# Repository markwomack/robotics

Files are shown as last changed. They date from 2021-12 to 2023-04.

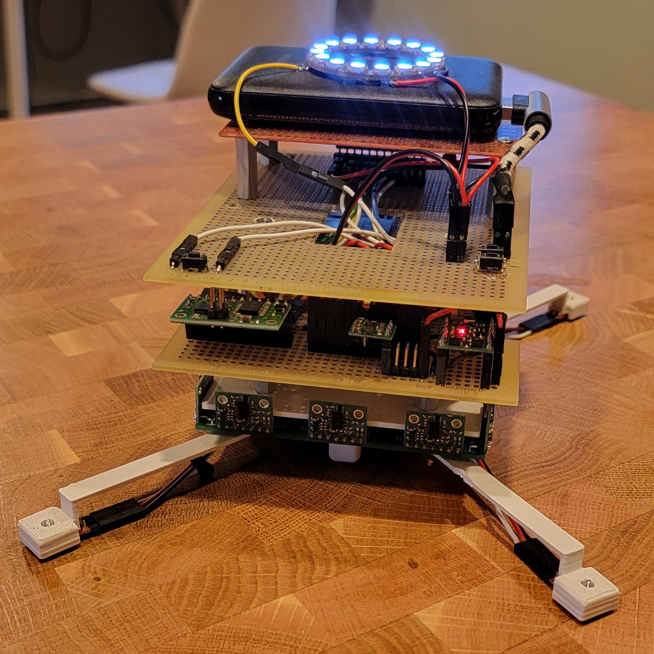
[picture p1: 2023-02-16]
robot_mark_ii/images/Beatrice_Portrait.jpg

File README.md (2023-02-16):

# robotics
The project stores the various designs, documentation, and code for my robots.

## ard_lib
This directory contains Arduino libraries that I have written and that I use in my robotics sketches. You can copy the directories in this folder to the Arduino "Libraries" directory and restart the Arduino IDE. Please see the [DEPENDENCIES](https://github.com/markwomack/robotics/blob/main/DEPENDENCIES.md) file for other Arduino library dependencies.

## robot_mark_ii
This directory contains all the Arduino sketches that I have written for my "Robot Mark II", the second robot iteration that I have built. The codename for this robot is "Beatrice". There are many test sketches to test the connections and functionality of the various sensors and motors. The "base_sketch" is the main sketch that has the behaviors I have written to run useful things on the robot.

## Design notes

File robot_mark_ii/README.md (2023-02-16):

# Robot Mark II 'Beatrice'
<p>This is the directory that contains all of the code and designs specific to the
Robot Mark II 'Beatrice'.</p>

* Beatrice is an all-around robot with many different
sensor sets that allow it to detect table edges, objects that are close by,
and lines that are placed on a table or floor.

* It is a differential drive robot
with motor encoders. This means that it has software control for the motor power
(PID) so that the motors perform at an expected rate of speed.

* The framework provided from using the
[Task Manager library](https://github.com/markwomack/TaskManager) and implemented
support classes means that it can be easily extended to perform different
behaviors.

* Printing debug messages to a remote computer allows for basic feedback when
debugging new bahaviors. This is done by using UDP over WiFi with the
[Arduino Logging library](https://github.com/markwomack/ArduinoLogging).

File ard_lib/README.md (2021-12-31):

# ard_lib
This is a collection Arduino libraries used for the robotics sketches. Copy them to the Arduino Libraries directory and then re-launch the Arduino IDE.

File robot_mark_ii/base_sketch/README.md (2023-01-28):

# Base Sketch

This is the base sketch for the Mark II 'Beatrice' robot that supports all of the behaviors
it has been programmed to perform. Beatrice is meant to be an all-around robot for 
different challenges such as the
[HBRC TableTop and A-Mazing LineBot challenges](https://www.hbrobotics.org/index.php/challenges/).
Beatrice is still a work-in-progress, and more behaviors will be added as they are
implemented.

## Files

### base_sketch.ino
<p>This sketch is the base of the program. It sets up all of the sensors, motors,
and leds that will be used on the robot. It creates the specific BehaviorTask that
will be executed, and uses the Task Manager to monitor a button to start/stop the
robot execution.</p>

### robot_constants.h
<p>This file contains the constants related to the robot, mostly physical constants
like the number of encoder ticks per wheel revolution, etc.</p>

### pin_assignments.h
<p>This file contains all of the Teensy 3.5 pin assignments used throughout the
code.</p>

### Behaviors
<p>The robot can be programmed to execute 'behaviors'. These behaviors can be anything
that it can use its sensors and output controls to perform.</p>

#### BehaviorTask
<p>The BehaviorTask is the base class for all of the behaviors that can be executed
on the robot. It has common members and methods that can be used by all subclasses
to implement their specific behavior.</p>

#### StayOnTableTopTask
<p>The StayOnTableTopTask is the behavior that will keep the robot on the table and
not fall off. Once it finds a table edge, the robot will go back and forth on the table.
It passes
[Phase 1 of the HBRC TableTop Challenge](https://www.hbrobotics.org/index.php/challenges/).</p>

#### PushOffTableTopTask
<p>The PushOffTableTopTask is the behavior that will search for an object, and when found
it will proceed to push the object off of the table. After pushing off the table, the
robot will do a happy dance and then wait to be activated again. It passes
[Phase 2 of the HBRC TableTop Challenge](https://www.hbrobotics.org/index.php/challenges/).</p>

### Sensors and Controls
<p>The robot has a number of sensors and output controls that it can use from its behaviors.</p>

#### EdgeSensors
<p>Edge sensors are used to detect the edges of the table, and are the four IR sensors located on
the four arms that come from the corners of the robot. The EdgeSensor class defines the methods
that can be used to initialize and access the sensor values.</p>

#### DistanceSensors
<p>Distance sensors are the ten sensors that ring the robot, two sets of 5. These are ToF
sensors that return a distance when an object is close. The DistanceSensors class defines the
methods that can be used to initialize and access the sensor values.</p>
  
#### MotorsAndEncoders
<p>There are two motors on the robot, each with its own encoders to know how far a wheel has
turned and thus how far the robot has travelled. The MotorsAndEncoders class defines the
methods that can be used to initialize and control the motors and encoders.</p>

#### PixelRing
<p>The robot has an Adafruit NeoPixel ring installed that can be used to indicate state
by the behavior implementation. The PixelRing class defines the methods and to
initialize and control the pixel ring.</p>

#### SurfaceSensors
<p>There are 10 surface sensors on the bottom of the robot. These are meant to detect things
on the surface of the table, such as lines of black tape. The SurfaceSensors class defines
the methods to initialize and access the sensor values.</p>

### Support Tasks
<p>There are a number of tasks used by the behavior tasks to help in reading sensors or
updating output controls. Each behavior task implementation can install whichever support
tasks it needs.</p>

#### AdjustMotorSpeedTask
<p>The AdjustMotorSpeedTask is called periodically to allow the motor PID controls, found
in the MotorsAndEncoders class, to adjust the power to the motors so that the target
speed is maintained.</p>

#### AdjustPixelRingTask
<p>Many of the defined patterns that can be shown on the PixelRing are animated. The
AdjustPixelRingTask allows the PixelRing to update its LEDs.</p>

#### ReadEdgeSensorsTask
<p>The ReadEdgeSensorsTask allows the robot to periodically read the values of the
edge sensors.</p>

### Miscellaneous

#### NetworkHub
<p>Optionally, the robot can be connected to WiFi to aid in debugging. The NetworkHub class
is used to connect to a WiFi network. The WiFi netword name and login credentials are stored
in the file secrets.h.</p>

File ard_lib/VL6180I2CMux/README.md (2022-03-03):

# VL6180I2CMux
<p>The VL6180I2CMux library provides code for accessing and managing the custom PCB used to manage up to 5 VL6180X Time-of-flight
  I2C distance sensors on an I2C bus. The VL6180X sensors use a single I2C address, and will conflict one another if placed on the
  same I2C bus. To remedy this situation, a simple multiplexer ship is used on the custom PCB to allow for a single sensor to be
  active at any time. Simply select the sensor you want to access before accessing it. In addition, the VL6180I2CMux library contains
  methods for accessing the sensor. However, once selected, you should be able to access the sensor on the I2C bus as you would normally.</p>

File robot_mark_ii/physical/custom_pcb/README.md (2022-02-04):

# Custom PCBs

This directory has files for custom PCBs used in the build of the Mark II 'Beatrice' robot.

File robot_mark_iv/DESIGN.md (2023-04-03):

# Design - Robot Mark IV 

This document outlines the design of the Mark IV robot.

## Components

These are the major components that make up the robot. This list does not have incidentals like protoboards, sockets, pins,
spacers, connectors, and wires.

- microcontroller tbd
- motorcontroller tbd
- 
- 2 - [Pololu Micro metal gear motor MP 6v 150:1](https://www.pololu.com/product/2382)
- 1 - [Pololu Gearmotor bracket (pair)](https://www.pololu.com/product/989)
- 1 - [Pololu Wheel 70x8mm (pair)](https://www.pololu.com/product/1425)
- 1 - [Pololu Magnetic encoder kit (pair)](https://www.pololu.com/product/4760)
- 2 - [Pololu 6-pin Single-ended Female cable (JST-SH)](https://www.pololu.com/product/4762)
- 2 - [Pololu 4mm x 15 IR sensors](https://www.pololu.com/product/4115)
-  distance sensors TBD
- 1 - [3000mAh Slim USB power bank](https://www.amazon.com/gp/product/B07K9HJR4X/)
- 1 - [USB C U Shape Adapter](https://www.amazon.com/gp/product/B09ZHFWZR9/)
- 1 - [Adafruit AirLift ESP32 WIFI Co-Processor](https://www.adafruit.com/product/4201)

Possible touchscreens:

[https://www.waveshare.com/2.13inch-Touch-e-Paper-HAT.htm](https://www.waveshare.com/2.13inch-Touch-e-Paper-HAT.htm)

[https://www.adafruit.com/product/2478](https://www.adafruit.com/product/2478)

### Chassis

### Microcontroller

### Motor controller

### Motors and encoders

### Power

### WIFI (optional, but recommended)

### Sensors

#### Distance Sensors

#### Line Tracking Sensors

### Robot Control

### State display

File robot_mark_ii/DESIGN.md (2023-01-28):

# Design - Robot Mark II - 'Beatrice'

This document outlines the design of the Mark II 'Beatrice' robot.

## Components

<p>These are the major components that make up Beatrice. This list does not have incidentals like protoboards, sockets, pins,
spacers, connectors, and wires. A wiring diagram is be provided, but how the components and wiring is arranged is left as
an exercise to the reader.</p>

- [Teensy 3.5 microcontroller](https://www.pjrc.com/store/teensy35.html)
- [Pololu Qik 2s9V1 motor controller](https://www.pololu.com/product/1110)
- [Polulu Micro metal gearmotor 12v 250:1 (2)](https://www.pololu.com/product/3055)
- [Pololu magnetic motor encoders (2)](pololu.com/product/2598)
- [Pololu 32x7mm wheels (2)](https://www.pololu.com/product/1087)
- [Pololu Gearmotor brackets (2)](https://www.pololu.com/product/1089)
- [Pololu Mini pushbutton power switch](https://www.pololu.com/product/2808)
- [Pololu 5v step-up/step-down voltage regulator](https://www.pololu.com/product/2119)
- [Pololu 7.5v step-up voltage regulator](https://www.pololu.com/product/4014)
- [Pololu IR sensors (4 total for edge detection)](https://www.pololu.com/product/2459)
- [Poloul IR sensors (2 total for line detection)](https://www.pololu.com/product/961)
- [Pololu VL6180X Time-of-Flight Distance Sensor (10)](https://www.pololu.com/product/2489)
- [Adafruit NeoPixel ring 16x5050](https://www.adafruit.com/product/2855)
- [5v power bank battery](https://www.amazon.com/gp/product/B07K6HJTK2)
- [USB cable slim connector](https://www.amazon.com/gp/product/B01MZ8RA3A)
- [Pololu mini pushbutton switch (2)](https://www.pololu.com/product/1400)
- [Adafruit AirLift ESP32 WIFI Co-Processor](https://www.adafruit.com/product/4201)

### Chassis

<p>The chassis is a collection of 3D printed parts for the mounted sensors, a couple of custom PCB boards, and several protoboards
  all put together to form the body of the robot. The chassis is designed to be symmetrical along the axis of the differential drive
  wheels. The profile and sensors of the robot are the same, front to back, flipping on the wheel axis. One side has been arbritrarily
  chosen to be the 'front', but future coding could treat each side equally, eliminating any need for the robot to turn around,
  instead just switching the 'front' in the software.</p>
  
### Microcontroller

<p>The Teensy 3.5 is the heart of the robot. It drives all of the sensors and behaviors.</p>
<p>The Teensy has been modified to use it's own power supply instead of relying on power from the USB port. This is [documented
  here](https://www.pjrc.com/store/teensy35.html) on the back side of the pinout card (see the "VIN separated from VUSB" note). 
  Be sure to do this when assembling the robot.</p>
<p>As of today the Teensy 3.5 may be discontinued (though I have been able to find it at a local MicroCenter). The newer
  Teensy 4.1 is almost a drop in replacement, however there are two issues to be aware of. First, while the Teensy 4.1 has the
  same pin form factor, but the pins are arranged differently. You will have to take this into account when wiring, and the 
  pin_assignments.h file in the code will need to be updated accordingly. Second, the Teensy 4.1 pins are NOT 5v tolerant as 
  they are for the 3.5. You will have to use 3.3v for all of the connections, and will need to have a 3.3v voltage regulator
  instead of the 5v voltage regulator. [Pololu provides a 3.3v voltage regulator](https://www.pololu.com/product/2122).
  Though I have not tried it as of yet, all of the electronic components should function correctly using 3.3v instead of 5v.</p>

### Motor controller

<p>The Pololu Qik 2s9v1 motor controller is a simple to use controller that can drive two motors. It uses a serial port to
  receive motor commands, and one of the Teensy serial ports is dedicated to the Qik. While the controller run on 5v,
  it provides for a separate power source to the motors, which on this robot is 7.5v (see Power section below).</p>

### Motors and encoders

<p>The Pololu micro metal gearmotors can handle up to 12v, but Beatrice runs them with just 7.5v. The motors have a 250:1
gear ratio, which will provide a lot of torque to the wheels to help Beatrice get over bumps and ridges. With the mini 
magnetic encoders having 12 ticks per shaft revolution with the 250:1 gear ratio, there will be 3000 ticks per wheel
revolution. This will provide a high level of accuracy in the odometry.</p>
<p>Beatrice uses a differential drive centered in the chassis. This allows the robot to move forward, backward, turn, and
  spin in place.</p>

### Power

<p>The power to Beatrice is provied by a 5v power bank connected via a modified USB cable to the 5v pushbutton power switch.
The power bank can provide up to 2A of current. The pushbutton switch provides reverse voltage protection. The power flows to
the robot from the switch to two different voltage regulators. The 5v regulator provides power to all of the electronics:
the Teensy, the Qik, and all of the sensors. The 7.5v regulator steps up the 5v to 7.5v to provide more power to the motors.
The 7.5 regulator is connected to the Qik motor controller, which passes the power to the motors.</p>
<p>The 5v regulator can deliver up to 1A in current which is more than sufficient for the electronics. The 7.5v regulator
can provide up to 3A current which much greater than the motor stall current of .75A (1.5A for both motors combined).</p>

### WIFI (optional, but recommended)

<p>Beatrice connects to the internet via the Adafruit ESP32 WIFI Co-Processor breakout board. It is connected to the Teensy
  through the SPI interface, and a custom Adafruit version of the Arduino WiFiNINA library is used to allow different pin
  locations. The internet connection is used to send debugging messages to a remote console, which greatly aids in the
  writing and debugging of robot behaviors. It is much harder to sense objects or program movement with a USB cable
  connected to the back of the robot's Teensy. However, this portion of the build is optional, but greatly recommended.
  Please see the ArduinoLogging library for an example of a setup on a remote computer to receive messages from the robot.</p>

### Sensors

<p>Beatrice is outfitted with different sets of sensors, each for a different purpose.</p>

#### Edge Sensors

<p>Extending out from each corner of the robot are 4 Pololu IR sensors, one for each corner. These are meant to detect
  edges of the tabletop on which the robot is operating. There is no special calibration performed for these sensors.
  Once the value goes above a certain threshold and 'edge' is detected. Each sensor is directly connected to a pin on
  the Teensy, which reads the value periodically when required by the behavior.</p>

#### Distance Sensors

<p>Wrapping around the robot are 10 VL6180X Time-of-Flight distance sensors (3 front, 3 rear, 2 right, 2 left). These
  are meant to detect objects in proximity to the robot. The maximum range of the VL6180X is 60cm, but in practice it
  is more in the 20-30cm range. Each sensor is an I2C device, and values are requested and read using the I2C bus.
  Unfortunately, each sensor hasthe same I2C address, which in turn requires a Multiplexer chip to select the specific
  sensor before interacting with it. For Beatrice this is done using a custom PCB board that is designed to have the
  multiplexer chip and 5 sensors mounted directly on the board. The board is then incorporated into the body of
  the chassis. There is one PCB for the front, and one PCB for the rear, with matching configurations. A separate
  I2C bus and set of selector pins on the Teesny are used to control each board in turn. While the sensors could be
  configured to run in 'continous' mode, currently the code samples distance measurements as needed for the specific
  task in hand. This avoids a periodic task running over its alloted time to execute, and overlapping signals each
  sensor sends out to measure distance. Future code could be written to better time the measurments for each
  sensor so that they do not intefere with each other.</p>

#### Line Tracking Sensors

<p>Underneath the robot, mounted on a 3D printed under-carriage, are more Pololu IR sensors. These are meant to detect
  line patterns on the tabletop or a maze. There are 10 sensors in total, arranged in lines: 2 at the front, 6 across
  the center, and 2 more at the rear. This arrangement makes detecting horizontal and vertical line patterns more
  efficient. Similar to the edge sensors, each sensor is connected to a pin on the Teensy. However, unlike the edge
  sensors, the line sensors require some level of calibration before use to detect lines. While calibrating, the robot
  needs to be moved over the lightest and darkest values found on the tabletop or maze. Once the calibration is completed,
  the calibrated values will then be used in detecting lines.</p>

### Robot Control

<p>The 5v pushbutton power switch will turn Beatrice on and off, but there are is another button to actually control
  the start and stop of the robot behavior. Beatrice uses the TaskManager library to monitor a pin on the Teensy that
  is connected to this pushbutton. When first turned on Beatrice will be in idle mode, with the PixelRing pulsing white.
  When the pushbutton is pressed, the programmed behavior will start. When the pushbutton is pressed again, the behavior
  will be stopped. Pushing the button again will start the behavior, now initialized to forget the previous execution.</p>
<p>Because Beatrice can perform several different behaviors, there is another push button that can be used to select the
  behavior to execute next time the start button is pressed. Each behavior type is numbered, and when selecting, the
  selected behavior number is displayed on the PixelRing by the matching number of LEDs.</p>
  
### State display

<p>Beatrice uses the Adafruit PixelRing to display its current state. When idle it will pulse white. While running it will
  update the PixelRing as it executes the behavior.

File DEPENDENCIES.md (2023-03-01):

# Dependencies

## Third Party Dependencies
The sketches and libraries have dependicies on some third party libraries.

- [MotorAndEncoderManager](https://github.com/markwomack/MotorAndEncoderManager) - Used
  drive the motors and encoders on the robots.
- [Pololu Qik controller](https://github.com/pololu/qik-arduino) - One of the motor
  controllers used.
- [Pololu VL6180X sensors](https://github.com/pololu/vl6180x-arduino) - The distance
  sensors used.
- [Pololu QTR sensors](https://github.com/pololu/qtr-sensors-arduino) - The edge and
  surface sensors used.
- [Adafruit NeoPixel](https://github.com/adafruit/Adafruit_NeoPixel) - The hardware used
  to communicate state.
- [Adafruit WiFiNINA](https://github.com/adafruit/WiFiNINA) - WiFi connction used for
  debugging purposes<br/>
**^^ MUST ^^** use the above version to allow different pin locations
- [PID controller](https://github.com/br3ttb/Arduino-PID-Library) - Used to precisely
  control the motor speeds.
- [PixelRingAnimator](https://github.com/markwomack/PixelRingAnimator) - Provides
  animations to run on the NeoPixel ring.
- [ArduinoLogging](https://github.com/markwomack/ArduinoLogging) - Used to print debug
  messages.
- [TaskManager](https://github.com/markwomack/TaskManager) - Used to manage the various
  tasks executed to run the robot behaviors.

Some of these libraries might already be installed in the Arduino
IDE, so check first.

## Local Dependencies
In addition to the above libraries, there are a number of 'local'
libraries that should also be installed to the Arduino environment.
They are located in the [ard_lib directory](https://github.com/markwomack/robotics/tree/main/ard_lib),
and can be copied directly to the Arduino library directory.

- [VL6180I2CMux](https://github.com/markwomack/robotics/tree/main/ard_lib/VL6180I2CMux) -
  The VL6180X ToF sensors used on Beatrice are accessed through I2C, but the address is
  hardcoded. This library allows for a multiplexer to be used to access each sensor as
  if it was the only one. There is 
  [specific hardware designed](https://github.com/markwomack/robotics/tree/main/robot_mark_ii/physical)
  to implement this feature and this code provides the methods to access it.

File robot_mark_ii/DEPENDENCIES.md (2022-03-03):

# Dependencies

<p>Besides all of the dependicies outlined elsewhere, Beatrice uses the [Teensy 3.5 microcontroller](https://www.pjrc.com/store/teensy35.html).
This means that you will need to install the TeensyDuino to your Arduino IDE in order for this code to compile correctly. Instruction on how
to install TeensyDuino can be [found here](https://www.pjrc.com/teensy/td_download.html).</p>

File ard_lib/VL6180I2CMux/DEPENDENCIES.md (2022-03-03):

# Dependencies

<p>The VL6180I2CMux library uses the [Pololu VL6180X library](https://github.com/pololu/vl6180x-arduino) to access the VL6180X sensors.</p>

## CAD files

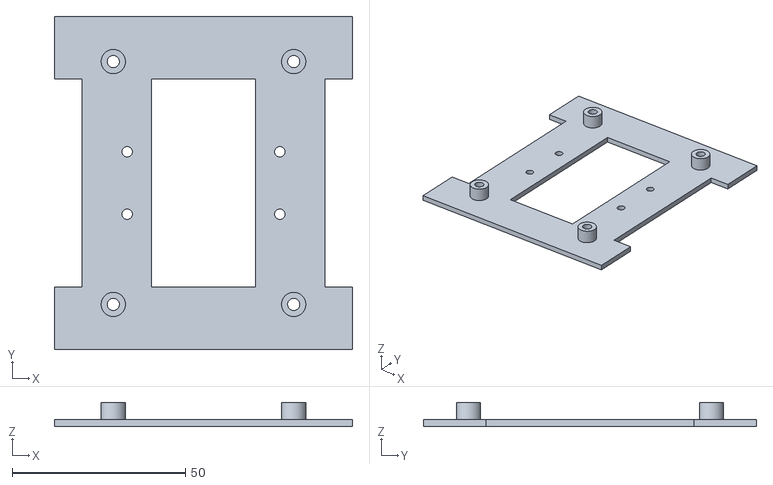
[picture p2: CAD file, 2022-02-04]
robot_mark_ii/physical/3d_printing/main_chassis.stl
86.0 x 96.0 x 7.00

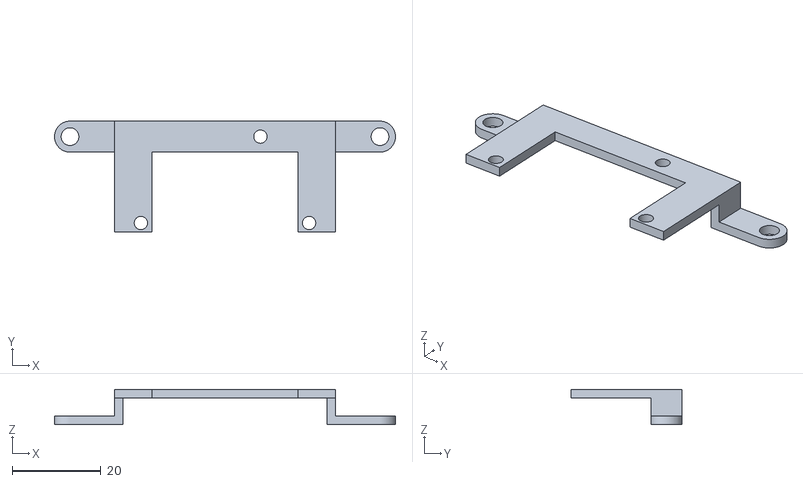
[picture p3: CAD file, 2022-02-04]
robot_mark_ii/physical/3d_printing/line_sensor_mount_left.stl
77.0 x 25.0 x 8.00

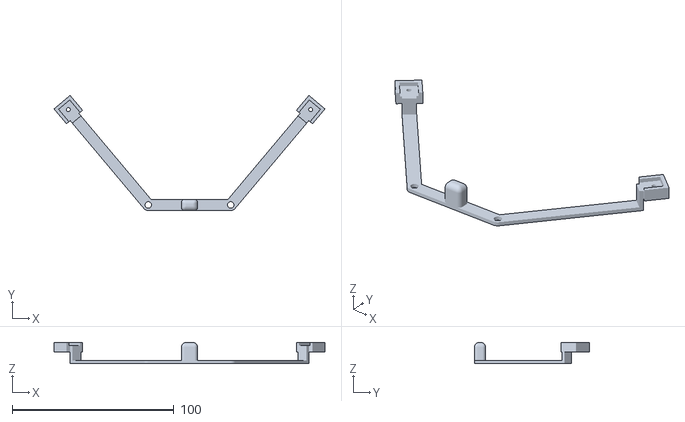
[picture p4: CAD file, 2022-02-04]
robot_mark_ii/physical/3d_printing/edge_sensor_mount_with_castor.stl
167.7 x 71.3 x 13.0

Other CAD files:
robot_mark_ii/physical/3d_printing/line_sensor_mount_right.stl

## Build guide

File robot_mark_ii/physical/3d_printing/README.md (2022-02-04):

# 3D Print Parts

This directory contains the custom parts for the Mark II 'Beatrice' robot that should be 3D printed.

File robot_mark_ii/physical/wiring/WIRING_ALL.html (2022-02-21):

# WIRING_ALL

## Diagram

## Bill of Materials

Id | Description | Qty | Unit | Designators
1 | Cable, 1 x 0.25 mm² | 0 | m | FL_IR_EDGE_DATA, FR_IR_EDGE_DATA, NEOPIXEL_DATA, PUSHBUTTON_START, QIK_RESET, RL_IR_EDGE_DATA, RR_IR_EDGE_DATA
2 | Cable, 2 x 0.25 mm² | 0 | m | F_IR_SURFACE_DATA, L_ENCODER_DATA, L_ENCODER_MOTOR_POWER, MUX_FRONT_I2C, MUX_REAR_I2C, POWER_7.5_VOLT, POWER_BATTERY, PULLSIGNAL_HIGH, PUSHBUTTON_POWER, QIK_SERIAL_DATA, R_ENCODER_DATA, R_ENCODER_MOTOR_POWER, R_IR_SURFACE_DATA
3 | Cable, 3 x 0.25 mm² | 0 | m | MUX_FRONT_DATA, MUX_REAR_DATA
4 | Cable, 6 x 0.25 mm² | 0 | m | AIRLIFT_CTRL, C_IR_SURFACE_DATA
5 | Connector, 12 pins | 1 | | Qik2s9v1
6 | Connector, 2 pins | 4 | | BatteryPack, PullSignalHigh, PushButton_Power, PushButton_Start
7 | Connector, 3 pins | 7 | | 5vVoltageRegulator, 7.5vVoltageRegulator, FrontLeft_IR_Edge_Sensor, FrontRight_IR_Edge_Sensor, NeoPixelRing, RearLeft_IR_Edge_Sensor, RearRight_IR_Edge_Sensor
8 | Connector, 4 pins | 2 | | Front_IR_Surface_Sensors, Rear_IR_Surface_Sensors
9 | Connector, 48 pins | 1 | | Teensy3.5
10 | Connector, 6 pins | 3 | | 5vPushButtonSwitch, LeftMotorEncoder, RightMotorEncoder
11 | Connector, 7 pins | 2 | | ToF_MUX_PCB_Front, ToF_MUX_PCB_Rear
12 | Connector, 8 pins | 2 | | AirLiftWIFI, Center_IR_Surface_Sensors
13 | Wire, 0.25 mm², BK | 0 | m | POWER_5_VOLT, POWER_INPUT
14 | Wire, 0.25 mm², RD | 0 | m | POWER_5_VOLT, POWER_INPUT

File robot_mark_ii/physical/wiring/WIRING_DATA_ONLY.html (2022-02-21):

# WIRING_DATA_ONLY

## Diagram

## Bill of Materials

Id | Description | Qty | Unit | Designators
1 | Cable, 1 x 0.25 mm² | 0 | m | FL_IR_EDGE_DATA, FR_IR_EDGE_DATA, NEOPIXEL_DATA, PUSHBUTTON_START, QIK_RESET, RL_IR_EDGE_DATA, RR_IR_EDGE_DATA
2 | Cable, 2 x 0.25 mm² | 0 | m | F_IR_SURFACE_DATA, L_ENCODER_DATA, MUX_FRONT_I2C, MUX_REAR_I2C, PULLSIGNAL_HIGH, QIK_SERIAL_DATA, R_ENCODER_DATA, R_IR_SURFACE_DATA
3 | Cable, 3 x 0.25 mm² | 0 | m | MUX_FRONT_DATA, MUX_REAR_DATA
4 | Cable, 6 x 0.25 mm² | 0 | m | AIRLIFT_CTRL, C_IR_SURFACE_DATA
5 | Connector, 12 pins | 1 | | Qik2s9v1
6 | Connector, 2 pins | 2 | | PullSignalHigh, PushButton_Start
7 | Connector, 3 pins | 6 | | 5vVoltageRegulator, FrontLeft_IR_Edge_Sensor, FrontRight_IR_Edge_Sensor, NeoPixelRing, RearLeft_IR_Edge_Sensor, RearRight_IR_Edge_Sensor
8 | Connector, 4 pins | 2 | | Front_IR_Surface_Sensors, Rear_IR_Surface_Sensors
9 | Connector, 48 pins | 1 | | Teensy3.5
10 | Connector, 6 pins | 2 | | LeftMotorEncoder, RightMotorEncoder
11 | Connector, 7 pins | 2 | | ToF_MUX_PCB_Front, ToF_MUX_PCB_Rear
12 | Connector, 8 pins | 2 | | AirLiftWIFI, Center_IR_Surface_Sensors
13 | Wire, 0.25 mm², BK | 0 | m | POWER_5_VOLT
14 | Wire, 0.25 mm², RD | 0 | m | POWER_5_VOLT

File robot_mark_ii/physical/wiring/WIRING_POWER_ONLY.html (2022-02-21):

# WIRING_POWER_ONLY

## Diagram

## Bill of Materials

Id | Description | Qty | Unit | Designators
1 | Cable, 2 x 0.25 mm² | 0 | m | L_ENCODER_MOTOR_POWER, POWER_7.5_VOLT, POWER_BATTERY, PULLSIGNAL_HIGH, PUSHBUTTON_POWER, R_ENCODER_MOTOR_POWER
2 | Connector, 12 pins | 1 | | Qik2s9v1
3 | Connector, 2 pins | 4 | | BatteryPack, PullSignalHigh, PushButton_Power, PushButton_Start
4 | Connector, 3 pins | 7 | | 5vVoltageRegulator, 7.5vVoltageRegulator, FrontLeft_IR_Edge_Sensor, FrontRight_IR_Edge_Sensor, NeoPixelRing, RearLeft_IR_Edge_Sensor, RearRight_IR_Edge_Sensor
5 | Connector, 4 pins | 2 | | Front_IR_Surface_Sensors, Rear_IR_Surface_Sensors
6 | Connector, 48 pins | 1 | | Teensy3.5
7 | Connector, 6 pins | 3 | | 5vPushButtonSwitch, LeftMotorEncoder, RightMotorEncoder
8 | Connector, 7 pins | 2 | | ToF_MUX_PCB_Front, ToF_MUX_PCB_Rear
9 | Connector, 8 pins | 2 | | AirLiftWIFI, Center_IR_Surface_Sensors
10 | Wire, 0.25 mm², BK | 0 | m | POWER_5_VOLT, POWER_INPUT
11 | Wire, 0.25 mm², RD | 0 | m | POWER_5_VOLT, POWER_INPUT

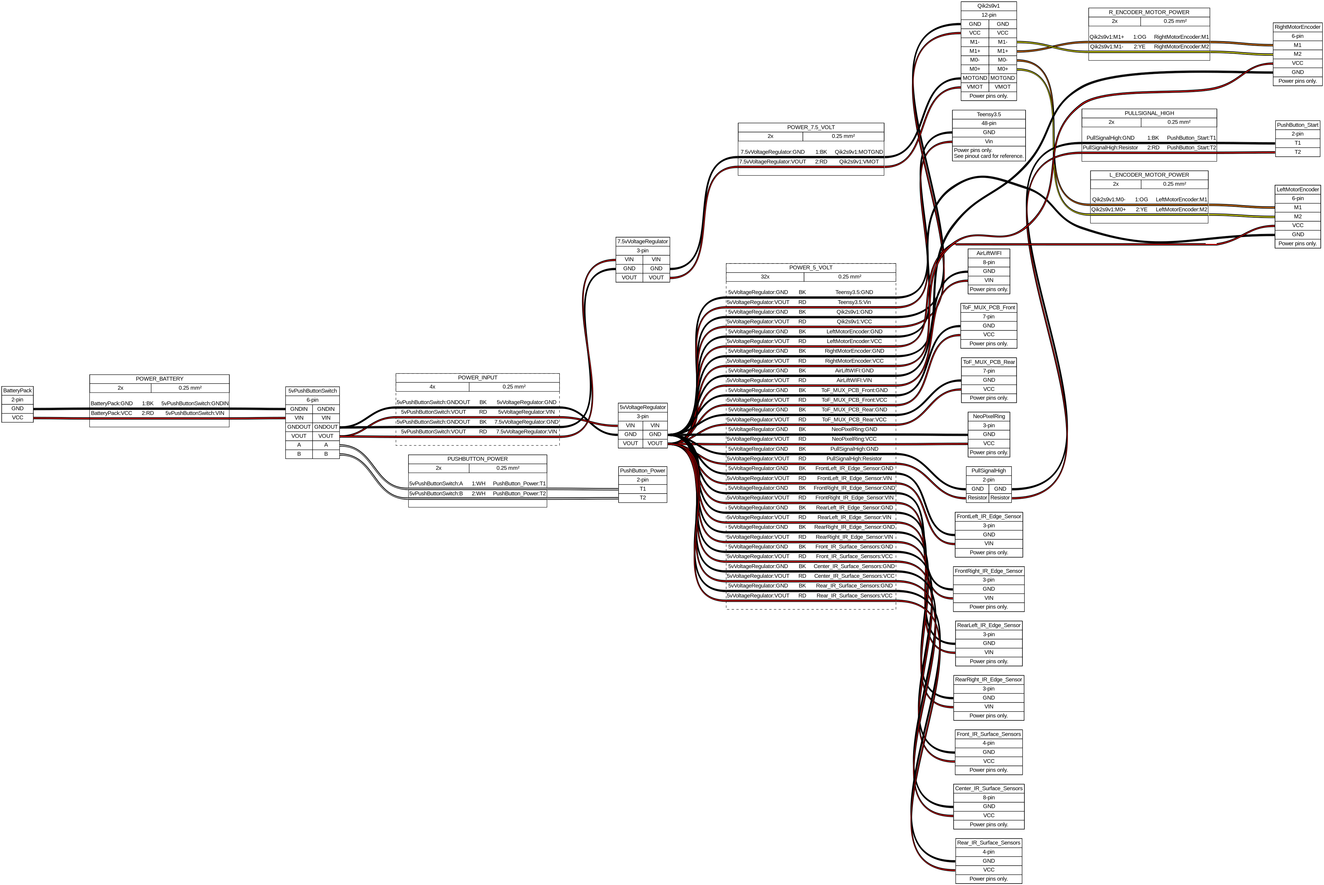
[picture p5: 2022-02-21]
robot_mark_ii/physical/wiring/WIRING_POWER_ONLY.png

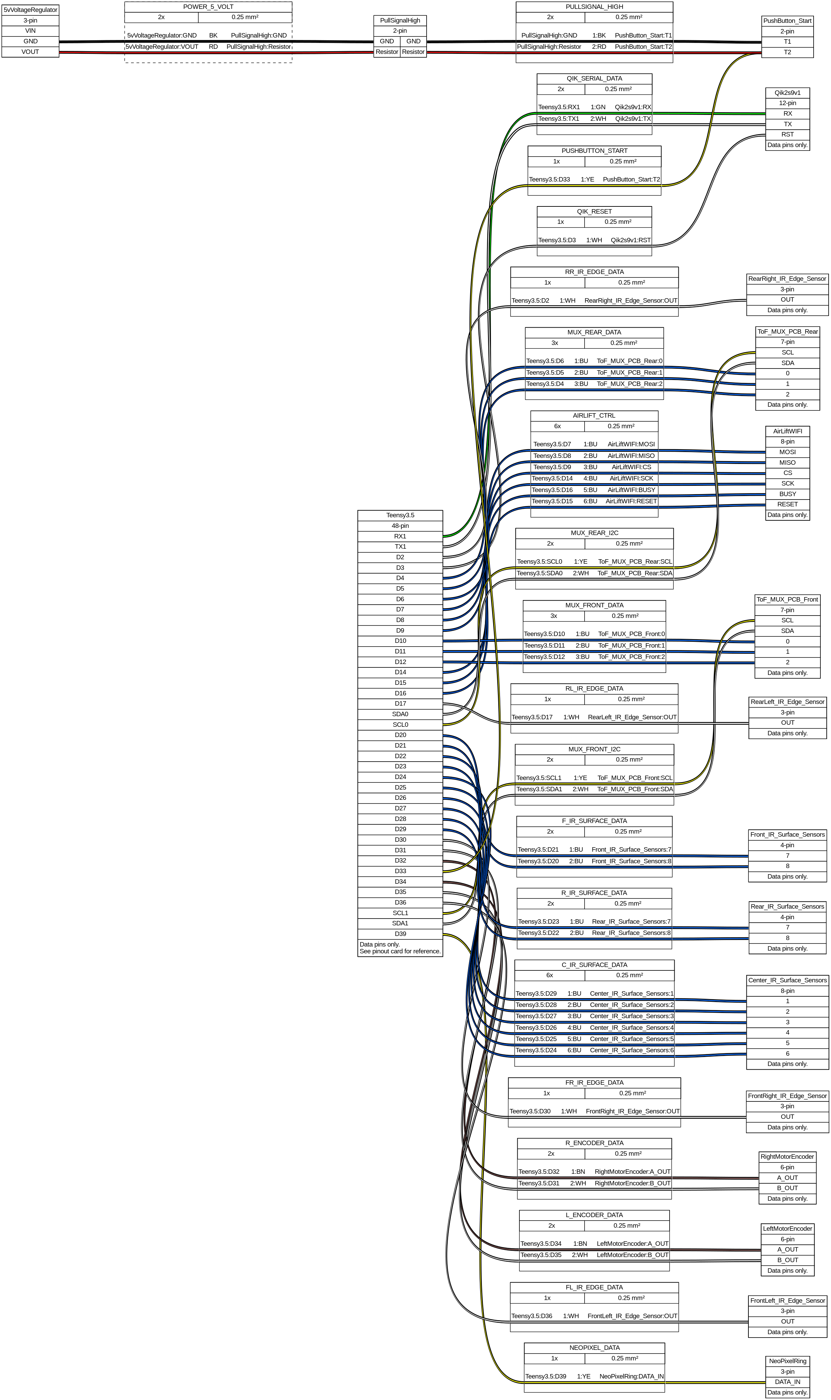
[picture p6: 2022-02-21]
robot_mark_ii/physical/wiring/WIRING_DATA_ONLY.png

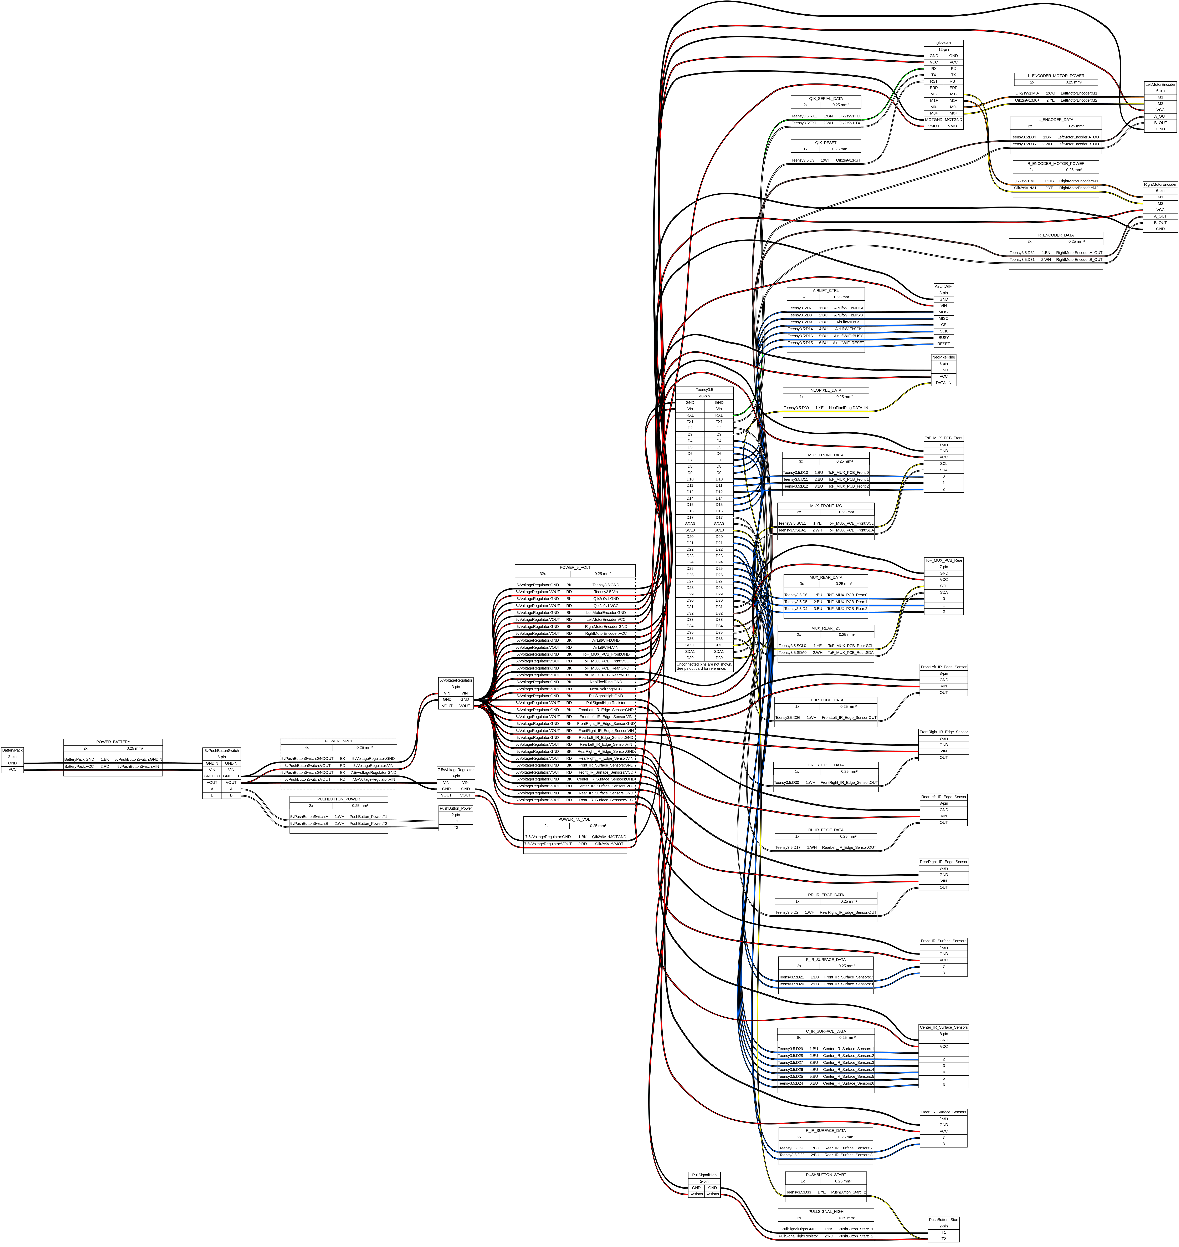
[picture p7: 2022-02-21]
robot_mark_ii/physical/wiring/WIRING_ALL.png

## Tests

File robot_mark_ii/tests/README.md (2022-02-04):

# Robot Mark II 'Beatrice' Test Sketches

These sketches can be used to "bring up" the various components of the robot
in isolation of the other components. You can test a component in isolation
to make sure it is functioning correctly. The pin assignments should be similar
or exactly like the assignments on the final robot. Double check to make sure.

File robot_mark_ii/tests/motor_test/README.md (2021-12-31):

# motor_test
This is an Arduino sketch to test and exercise the motors and motor encoders for the Robot Mark II.

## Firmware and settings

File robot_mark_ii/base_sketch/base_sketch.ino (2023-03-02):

//
// Licensed under Apache 2.0 license.
// See accompanying LICENSE file for details.
//

// Base Arduino includes
#include <Arduino.h>
#include <inttypes.h>

// My includes
#include <TaskManager.h>
#include <Task.h>
#include <DebugMsgs.h>
#include <UDPPrintWrapper.h>

// Local includes
#include "pin_assignments.h"
#include "globals.h"
#include "NetworkHub.h"
#include "DistanceSensors.h"
#include "EdgeSensors.h"
#include "MotorsAndEncoders.h"
#include "SurfaceSensors.h"
#include "Animation.h"
#include "BehaviorTask.h"
#include "StayOnTableTopTask.h"
#include "PushOffTableTopTask.h"
#include "AdjustAnimationTask.h"
#include "CalibrateSurfaceSensorsTask.h"

// Simple idle task to fade the pixel ring white
class IdleTask : public AdjustAnimationTask {
  public:
    IdleTask() {};
    
    void start(void) {
      _animation->setAnimationState(WHITE_FADE);
    };
};
IdleTask idleTask;

// All of the sensors, motors, and pixel ring
EdgeSensors edgeSensors;
DistanceSensors distanceSensors;
SurfaceSensors surfaceSensors;
MotorsAndEncoders motorsAndEncoders;
Animation animation;

// This is the behavior defined for the robot
BehaviorTask* behaviorTask;

// This is the hub that connects to the wider network
NetworkHub networkHub;

// Creates the behavior task to be executed
BehaviorTask* createBehaviorTask(void) {
  return new CalibrateSurfaceSensorsTask();
  //return new PushOffTableTopTask();
  //return new StayOnTableTopTask();
}

void setup() {
  Serial.begin(9600);
  
  DebugMsgs.disableAll();
  // Uncomment this line to enable debug msgs
  DebugMsgs.enableLevel(DEBUG);
   
  // Set up remote udp port debugging
  if (UDP_DEBUGGING) {
    if (networkHub.start() == 0) {
      DebugMsgs.println("Switching to debug messages through remote udp");
      
      UDPPrintWrapper* udpPrint =
        new UDPPrintWrapper(networkHub.getUdpPort(DEBUG_UDP_PORT), UDP_TARGET_ADDRESS, UDP_TARGET_PORT);
      
      DebugMsgs.setPrint(udpPrint);
      DebugMsgs.println("Starting debug messages through remote udp");
    } else {
      DebugMsgs.println("Error connecting to network, debug messages will continue local");
    }
  }

  // These are globals that need to be initialized
  // before the rest of the program
  edgeSensors.initialize();
  distanceSensors.initialize();
  surfaceSensors.initialize();
  motorsAndEncoders.initialize();
  animation.initialize();

  // get the behavior task to execute
  behaviorTask = createBehaviorTask();

  idleTask.setAnimation(&animation);
  
  // add tasks into the task manager
  taskManager.addIdleTask(&idleTask, 50);
  behaviorTask->setTaskToken(taskManager.addTask(behaviorTask, 10));

  // start monitoring the button to start the tasks
  taskManager.startMonitoringButton(BUTTON_PIN, HIGH);
}

void loop() {
  // Execute tasks
  taskManager.update();
}

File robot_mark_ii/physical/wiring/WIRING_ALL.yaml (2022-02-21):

connectors:
  BatteryPack:
    pins: [GND,VCC]
  
  5vPushButtonSwitch:
    pins: [GNDIN,VIN,GNDOUT,VOUT,A,B]
    
  5vVoltageRegulator:
    pins: [VIN,GND,VOUT]
    
  7.5vVoltageRegulator:
    pins: [VIN,GND,VOUT]
    
  Teensy3.5:
    pincount: 48
    pins: [GND,Vin,Analog GND,3.3V,RX1,TX1,D2,D3,D4,D5,D6,D7,D8,D9,D10,D11,D12,D13,D14,D15,D16,
    D17,SDA0,SCL0,D20,D21,D22,D23,D24,D25,D26,D27,D28,D29,D30,D31,D32,D33,D34,D35,D36,SCL1,SDA1,D39]
    hide_disconnected_pins: True
    notes: Unconnected pins are not shown.<br/>See pinout card for reference.

  Qik2s9v1:
    pins: [GND,VCC,RX,TX,RST,ERR,M1-,M1+,M0-,M0+,MOTGND,VMOT]
    
  LeftMotorEncoder:
    pins: [M1,M2,VCC,A_OUT,B_OUT,GND]
  
  RightMotorEncoder:
    pins: [M1,M2,VCC,A_OUT,B_OUT,GND]
  
  AirLiftWIFI:
    pins: [GND,VIN,MOSI,MISO,CS,SCK,BUSY,RESET]
    
  ToF_MUX_PCB_Front:
    pins: [GND,VCC,SCL,SDA,0,1,2]
  
  ToF_MUX_PCB_Rear:
    pins: [GND,VCC,SCL,SDA,0,1,2]
    
  FrontLeft_IR_Edge_Sensor:
    pins: [GND,VIN,OUT]
    
  FrontRight_IR_Edge_Sensor:
    pins: [GND,VIN,OUT]
    
  RearLeft_IR_Edge_Sensor:
    pins: [GND,VIN,OUT]
    
  RearRight_IR_Edge_Sensor:
    pins: [GND,VIN,OUT]
    
  RearRight_IR_Edge_Sensor:
    pins: [GND,VIN,OUT]
    
  Front_IR_Surface_Sensors:
    pins: [GND,VCC,7,8]
    
  Center_IR_Surface_Sensors:
    pins: [GND,VCC,1,2,3,4,5,6]
    
  Rear_IR_Surface_Sensors:
    pins: [GND,VCC,7,8]
    
  NeoPixelRing:
    pins: [GND,VCC,DATA_IN]
    
  PushButton_Power:
    pins: [T1, T2]
    
  PushButton_Start:
    pins: [T1, T2]
    
  PullSignalHigh:
    pins: [GND,Resistor]
    
cables:
  POWER_BATTERY:
    gauge: 0.25 mm2
    colors: [BK, RD]
    
  POWER_INPUT:
    category: bundle
    wirecount: 4
    gauge: 0.25 mm2
    colors: [BK, RD]
    
  POWER_5_VOLT:
    category: bundle
    wirecount: 32
    gauge: 0.25 mm2
    colors: [BK, RD]
    
  POWER_7.5_VOLT:
    gauge: 0.25 mm2
    colors: [BK, RD]
    
  QIK_SERIAL_DATA:
    gauge: 0.25 mm2
    colors: [GN, WH]
    
  QIK_RESET:
    gauge: 0.25 mm2
    colors: [WH]
  
  AIRLIFT_CTRL:
    gauge: 0.25 mm2
    wirecount: 6
    colors: [BU]
  
  NEOPIXEL_DATA:
    gauge: 0.25 mm2
    colors: [YE]
    
  L_ENCODER_MOTOR_POWER:
    gauge: 0.25 mm2
    colors: [OG,YE]
    
  L_ENCODER_DATA:
    gauge: 0.25 mm2
    colors: [BN,WH]
    
  R_ENCODER_MOTOR_POWER:
    gauge: 0.25 mm2
    colors: [OG,YE]
    
  R_ENCODER_DATA:
    gauge: 0.25 mm2
    colors: [BN,WH]
    
  MUX_FRONT_DATA:
    gauge: 0.25 mm2
    wirecount: 3
    colors: [BU]
    
  MUX_FRONT_I2C:
    gauge: 0.25 mm2
    colors: [YE,WH]
    
  MUX_REAR_DATA:
    gauge: 0.25 mm2
    wirecount: 3
    colors: [BU]
    
  MUX_REAR_I2C:
    gauge: 0.25 mm2
    colors: [YE,WH]
    
  FL_IR_EDGE_DATA:
    gauge: 0.25 mm2
    colors: [WH]
    
  FR_IR_EDGE_DATA:
    gauge: 0.25 mm2
    colors: [WH]
    
  RL_IR_EDGE_DATA:
    gauge: 0.25 mm2
    colors: [WH]
    
  RR_IR_EDGE_DATA:
    gauge: 0.25 mm2
    colors: [WH]
    
  F_IR_SURFACE_DATA:
    gauge: 0.25 mm2
    wirecount: 2
    colors: [BU]
    
  C_IR_SURFACE_DATA:
    gauge: 0.25 mm2
    wirecount: 6
    colors: [BU]
    
  R_IR_SURFACE_DATA:
    gauge: 0.25 mm2
    wirecount: 2
    colors: [BU]
    
  PUSHBUTTON_POWER:
    gauge: 0.25 mm2
    wirecount: 2
    colors: [WH]
    
  PUSHBUTTON_START:
    gauge: 0.25 mm2
    colors: [YE]
    
  PULLSIGNAL_HIGH:
    gauge: 0.25 mm2
    colors: [BK,RD]
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

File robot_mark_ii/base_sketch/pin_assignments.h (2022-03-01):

//
// Licensed under Apache 2.0 license.
// See accompanying LICENSE file for details.
//

#ifndef PIN_ASSIGNMENTS_H
#define PIN_ASSIGNMENTS_H

// Pin Definitions - Defines all of the pins used
const uint8_t POLOLU_QIK_TX_PIN        =  0; // tx Pololu qik
const uint8_t POLOLU_QIK_RX_PIN        =  1; // rx Pololu qik
const uint8_t RR_EDGE_SENSOR_PIN       =  2; // rear-right edge sensor
const uint8_t POLOLU_QIK_RESET_PIN     =  3; // reset Pololu qik
const uint8_t REAR_MUX_PIN2            =  4; // rear distance sensor mux selector pin 2
const uint8_t REAR_MUX_PIN1            =  5; // rear distance sensor mux selector pin 1
const uint8_t REAR_MUX_PIN0            =  6; // rear distance sensor mux selector pin 0
const uint8_t FRONT_MUX_PIN0           =  7; // front distance sensor mux selector pin 0
const uint8_t FRONT_MUX_PIN1           =  8; // front distance sensor mux selector pin 1
const uint8_t FRONT_MUX_PIN2           =  9; // front distance sensor mux selector pin 2
const uint8_t WIFI_SPI_CS0_PIN         = 10; // SPI CS0 used by Wifi
const uint8_t WIFI_SPI_MOSI0_PIN       = 11; // SPI MOSI0 uased by Wifi
const uint8_t WIFI_SPI_MISO0_PIN       = 12; // SPI MISO0 uased by Wifi
const uint8_t MODE_BUTTON_PIN          = 13; // mode button
const uint8_t WIFI_SPI_SCK0_PIN        = 14; // SPI SCK0 used by Wifi
const uint8_t WIFI_RESET_PIN           = 15; // reset pin used by Wifi
const uint8_t WIFI_BUSY_PIN            = 16; // busy pin used by Wifi
const uint8_t RL_EDGE_SENSOR_PIN       = 17; // rear-left edge sensor
                                     //= 18; // SDA0 I2C (aka Wire) connected to FRONT_MUX
                                     //= 19; // SCL0 I2C (aka Wire) connected to FRONT_MUX
const uint8_t FL_SURFACE_SENSOR_PIN    = 20; // front-left surface sensor
const uint8_t FR_SURFACE_SENSOR_PIN    = 21; // front-right surface sensor
const uint8_t RR_SURFACE_SENSOR_PIN    = 22; // rear-right surface sensor
const uint8_t RL_SURFACE_SENSOR_PIN    = 23; // rear-left surface sensor
const uint8_t CTR_SURFACE_SENSOR_6_PIN = 24; // center surface sensor 6
const uint8_t CTR_SURFACE_SENSOR_5_PIN = 25; // center surface sensor 5
const uint8_t CTR_SURFACE_SENSOR_4_PIN = 26; // center surface sensor 4
const uint8_t CTR_SURFACE_SENSOR_3_PIN = 27; // center surface sensor 3
const uint8_t CTR_SURFACE_SENSOR_2_PIN = 28; // center surface sensor 2
const uint8_t CTR_SURFACE_SENSOR_1_PIN = 29; // center surface sensor 1
const uint8_t FR_EDGE_SENSOR_PIN       = 30; // front-right edge sensor
const uint8_t ENCODER_R_PHASE_B_PIN    = 31; // right encoder phase b signal
const uint8_t ENCODER_R_PHASE_A_PIN    = 32; // right encoder phase a signal
const uint8_t BUTTON_PIN               = 33; // start/stop button
const uint8_t ENCODER_L_PHASE_B_PIN    = 34; // left encoder phase b signal
const uint8_t ENCODER_L_PHASE_A_PIN    = 35; // left encoder phase a signal
const uint8_t FL_EDGE_SENSOR_PIN       = 36; // front_left edge sensor
                                     //= 37; // SCL1 I2C (aka Wire1) connected to REAR_MUX
                                     //= 38; // SDA1 I2C (aka Wire1) connected to REAR_MUX
const uint8_t PIXEL_RING_PIN           = 39; // pixel ring data pin

#endif

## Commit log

2021-12-31 Initial checkin of arduino libraries.
2022-01-08 Fixed bug when printing uint8_t
2022-01-08 Adding test sketch and supporting library for VL6180 distance sensors
2022-01-08 Adding sketch to test distance sensors
2022-01-24 Final tweaks to distance sensor test code.
2022-01-24 Some final tweaks to the motor test code.
2022-01-24 Added tests for edge detection sensors.
2022-01-24 Added code for surface detection sensors.
2022-01-27 Added a MotorController that can be used to drive the robot using radians/sec for speed and PIDs to adjust the speed.
2022-01-27 Changes to use new MotorController class to control speed and drive in fairly straight lines.
2022-02-03 Added physical wiring diagrams.
2022-02-04 Added pcb files for VL6180_MUX pcb.
    [VL6180_MUX_Controller.fzz]
2022-02-04 Added 3D files for chassis and sensor mounts.
    [edge_sensor_mount_with_castor.stl, line_sensor_mount_left.stl, line_sensor_mount_right.stl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]
2022-02-05 Updated sensor count.
2022-02-07 Defined enum for motor
2022-02-07 Defined some new constants with the wheel and base circumference.
2022-02-21 Remove SerialDebug, should now use ArduinoLogging instead
2022-02-21 Added PushOffTableBehavior, use ArduinoLogging for debug msgs, updated pin assignments, added code to use remote UDP port for debug messages
2022-02-21 Updated wiring diagrams to include AirLift WIFI
2022-03-01 Updated to use external TaskManager library instead of ButtonExecutor.
2022-03-02 Update DESIGN.md
    Added sensor, robot control, state display sections, minor updates elsewhere.
2023-01-27 Update VL6180I2CMux.cpp
    Added a delay after selecting the sensors when initializing so that select/i2c has a change to be complete before calling init.
2023-02-07 Updated MotorManager to define MotorEncoder interface and implement QuadratureMotorEncoder
2023-02-08 Added basic BLDC manager and three phase encoder.
2023-02-08 Updated the BLDC example
2023-02-10 Tested with BLDCExample, added readFaults method to MotorEncoder interface.
2023-02-10 Use attachInterruptEx for better design and to allow unlimited encoders instead of just two.
2023-02-10 Uncommented code to switch direction
2023-02-12 Updated to use MotorAndEncoderManager library
2023-02-15 Updated to use the latest MotorAndEncoderManager library
2023-02-15 Removed MotorManager and MotorController ard_libs in favor of MotorAndEncoderManager library.
2023-02-26 Mostly updates to add calibrate sensors task with changes to pixel ring code.
2023-03-01 Fixed bug with idleTask not working after calibration task completed.
    [base_sketch.ino]
2023-03-01 Finished calibration task, started FollowLineTask, added ReadSurfaceSensorsTask
2023-03-02 Created some globals for sensors to make it better for every BehaviorTask have references to them
